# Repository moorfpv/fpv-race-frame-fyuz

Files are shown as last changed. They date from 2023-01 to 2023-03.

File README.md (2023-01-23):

# FYUZ - FPV Open Source 5" Race Frame

Bau dir deinen eigenen Race Copter für 16mm oder 12mm Lochkreis Motoren mit dem FYUZ Rahmenset. Die Carbon-Bauteile sind mit geringst möglichem Herstellungsaufwand zu produzieren.  

fyuz_s300

## Frame-Spec
* Propbase: 5"  
* Bottomplate: 2mm
* Midplate: 2mm
* Toplate: 2mm
* Armhook: 2mm or 3mm
* Arms: 4mm or 5.5mm
* AIO-Mount: 2mm, for M2, for 25.5 x 25.5 AIO Boards
* Lipopad: 2mm Moosgummi
* Stack mounting: 20 x 20 (for M2 or M3 screws)
* Standoff distance: 20mm
* Weight 5" with 20mm Alu Standoffs:  
  * with 4mm Arms for Motormount 12mm: 43.5g  
  * with 5.5mm Arms for Motormount 16mm: 56.2g  

## Carbon Parts

### 2mm Plate
* Bottomplate-H2.0.dxf  
* Midplate-M2-Stack-H2.0.dxf  
* Midplate-M3-Stack-H2.0.dxf  
* Topplate-H2.0.dxf  
* AIO-Mount-M2-StackMount-H2.0.dxf  
* Armhook-H2.0.dxf (Motormount 12mm)  

### 3mm Plate
* Armhook-H3.0.dxf (Motormount 16mm)  

### 4mm Arms
* 4x-715.70-H4.0.dxf (Motormount 12mm)  

### 5.5mm Arms
* 4x-720.76-H5.5.dxf (Motormount 16mm)  

## Buy Carbon - only Top producer/dealer
* [AHLtec](https://www.ahltec.de/shop/de/); optional mit Fräs-Service - Germany  
* [www.ikabon.com](https://www.ikabon.com); [email, Wendy Chan](mailto:info@ikabon.com) - China  
* [www.jinjiuyi.net](http://www.jinjiuyi.net); [email](mailto:info@jinjiuyi.net) - China  

## Laser Parts
* LipoPad.dxf

## Screws & Nuts

* countersunk head screw 4x M3 x 16  
* countersunk head screw 4x M3 x 6  
* pressnut 6x M3; [Buy](https://www.copterfarm.de/einpressmuttern-m3-10er-set-521.html) - Germany  

### For Fyuz Sub300 - Motormount 12mm
* countersunk head screw 2x M3 x 10

### For Fyuz - Motormount 16mm
* countersunk head screw 2x M3 x 12

### For AIO Mount
* lens head screw 4x M2 x 12 | 8 | 6

# Betaflight Presets - EXPERIMENTAL
* [BF 4.3 Presets for FyuzS300](https://github.com/moorfpv/betaflight-presets)
* [How to use Presets](https://betaflight.de/docs/knowledge-base/hintergrundwissen/betaflight-presets/)

# License

Creative Commons (4.0 International License) Attribution - NonCommercial - Share Alike (https://creativecommons.org/licenses/by-nc-sa/4.0/deed.en)

This work (DXF-Files) is licensed under a [Creative Commons (4.0 International License) Attribution - NonCommercial - Share Alike](https://creativecommons.org/licenses/by-nc-sa/4.0/deed.en).  

✖ | Sharing without ATTRIBUTION  
✔ | Remix Culture allowed  
✖ | Commercial Use  
✖ | Free Cultural Works  
✖ | Meets Open Definition  

# See also
* [Fyuz S300 Printables](https://www.printables.com/model/322457-sub300fpv-fyuz/files)  
* [screwsandmore](https://www.screwsandmore.de/en) - Germany  
* [five33 Printables](https://www.printables.com/model/243738-five33-lightswitch)  

---



* Arms: 4mm  
* Armhook: 2mm
* Weight 5" with 20mm Alu Standoffs: 43.5g  

Sources: [Arm-Parts/Motormount-12mm](https://github.com/moorfpv/fpv-race-frame-fyuz/tree/master/Arm-Parts/Motormount-12mm)  

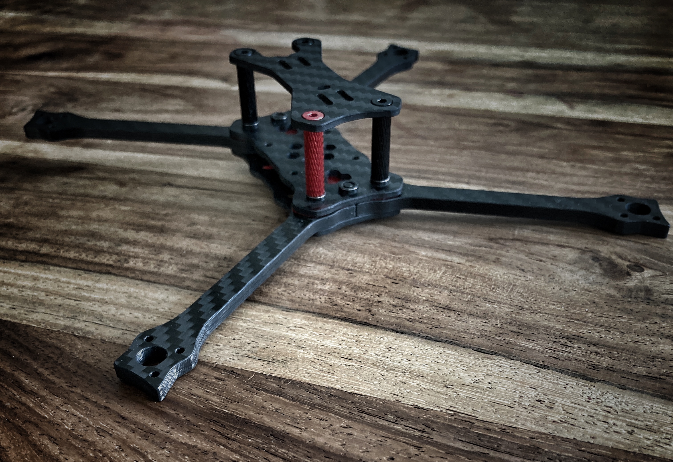
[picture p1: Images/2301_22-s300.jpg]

---
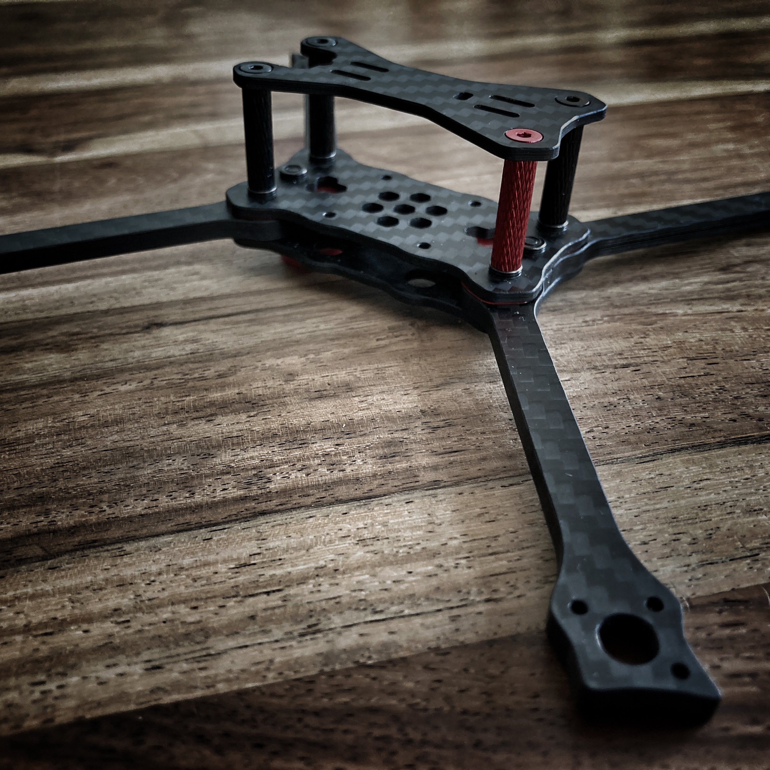
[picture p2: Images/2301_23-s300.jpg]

---


---  
---  



* Arms: 5.5mm  
* Armhook: 3mm
* Weight 5" with 20mm Alu Standoffs: 56.2g  

Sources: [Arm-Parts/Motormount-16mm](https://github.com/moorfpv/fpv-race-frame-fyuz/tree/master/Arm-Parts/Motormount-16mm)  

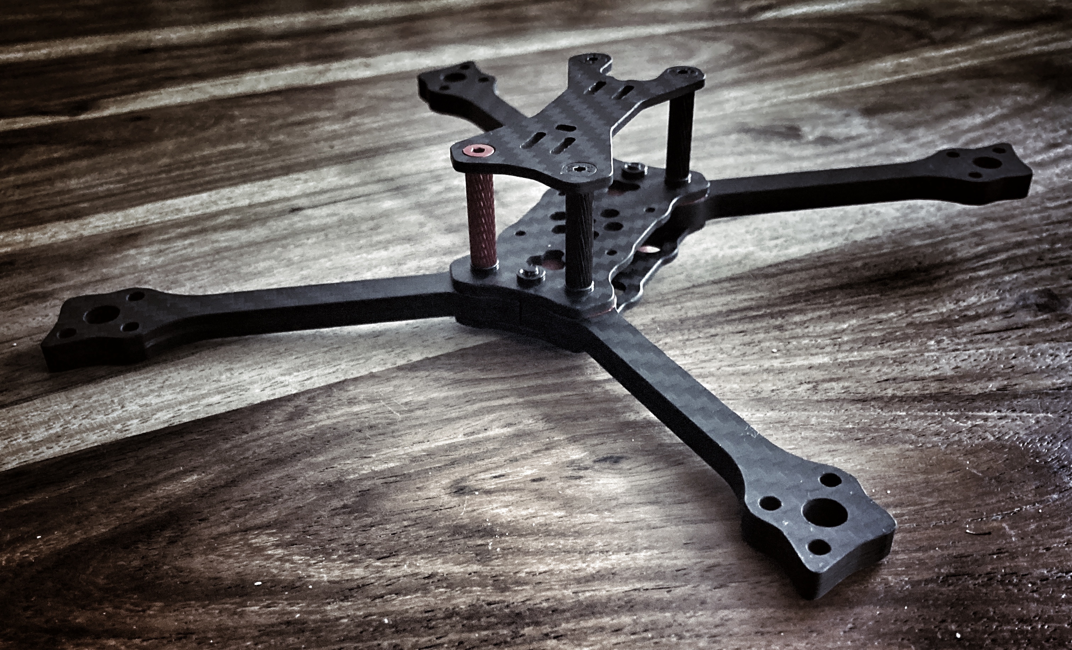
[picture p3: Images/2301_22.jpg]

---
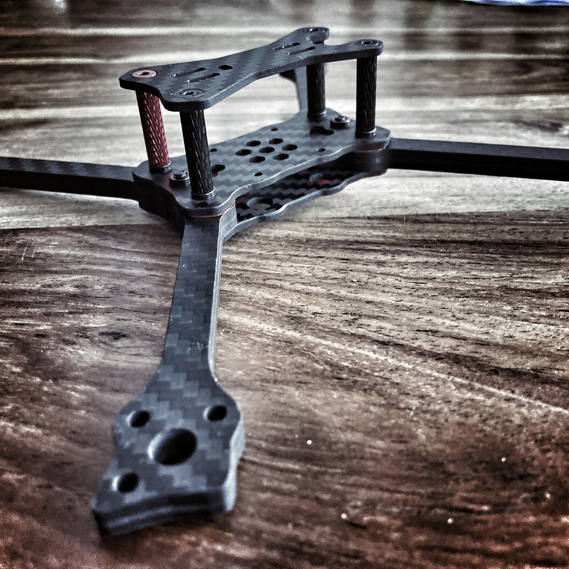
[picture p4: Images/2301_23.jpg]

---


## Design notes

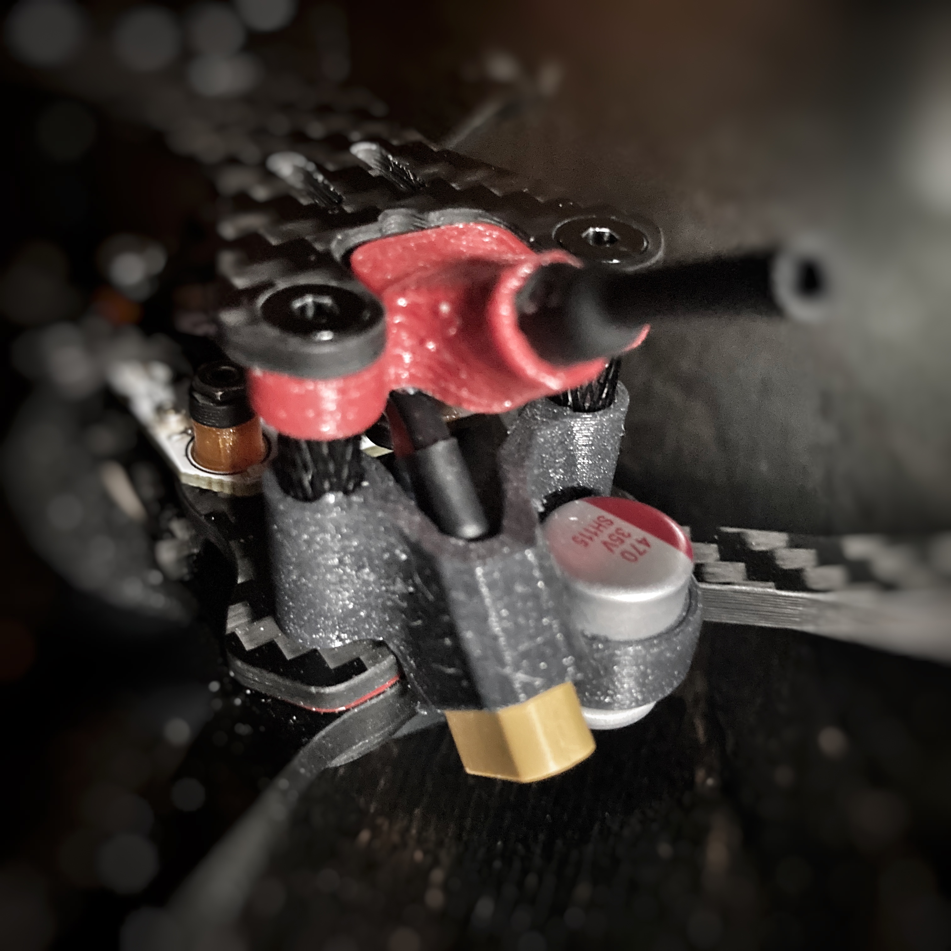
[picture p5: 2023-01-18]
Images/2301_02-s300.jpg

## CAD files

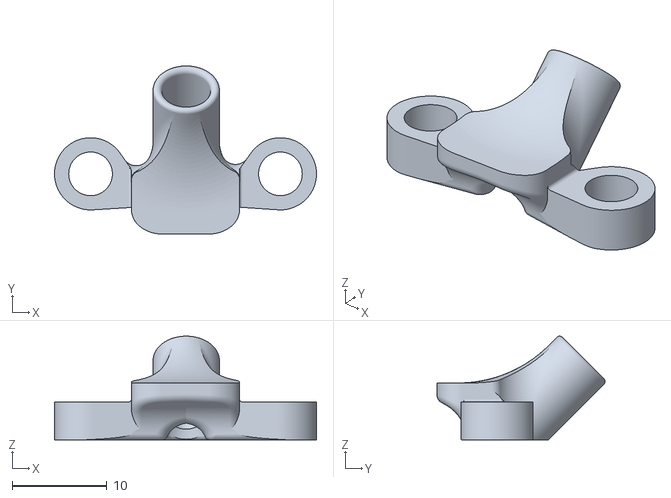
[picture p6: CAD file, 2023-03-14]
3D-Parts/TPU/Fyuz-TBS-Linear-VtxAntenna-Mount-v2.1.stl
27.6 x 17.7 x 10.9

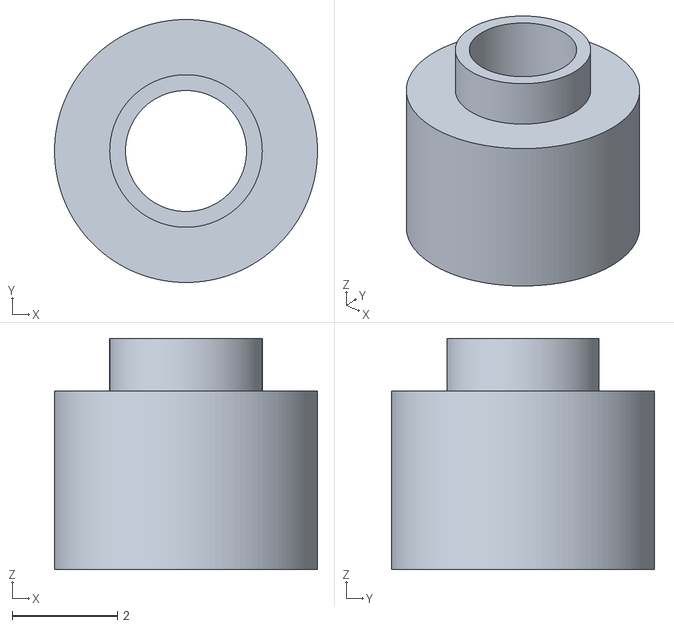
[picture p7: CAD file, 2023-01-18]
AIO-Mount/3D-Parts/ASA_Nozzle-0.2/AIOmount-Spacer-M2-H3.4.stl
5.00 x 5.00 x 4.40

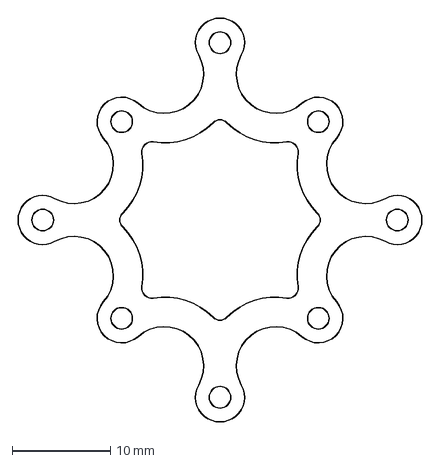
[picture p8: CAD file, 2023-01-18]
AIO-Mount/CNC-Parts/AIO-Mount-M2-StackMount-H2.0.dxf
41.4 x 41.4 mm

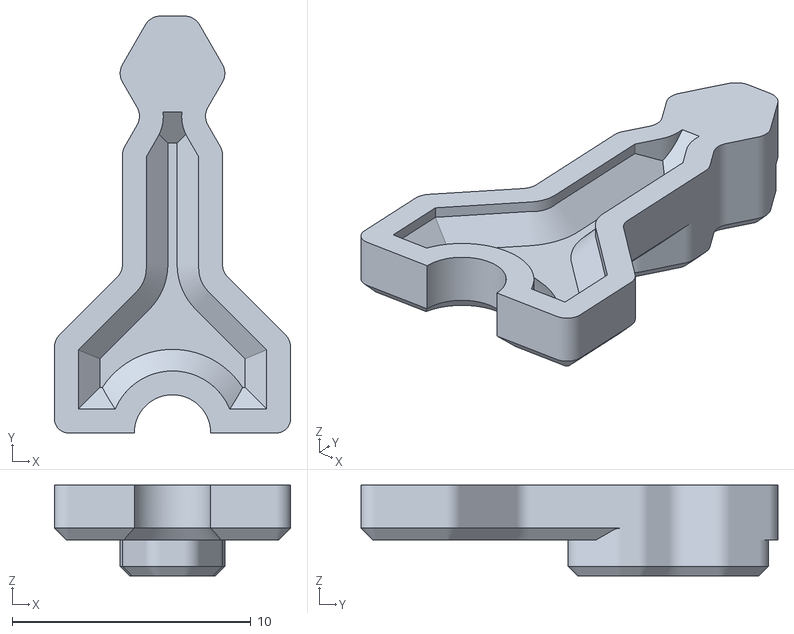
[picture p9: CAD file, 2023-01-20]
Arm-Parts/Motormount-12mm/3D-Parts/TPU/Peezer-v2-Armhook-H2.0-Arm-H4.0.stl
9.90 x 17.5 x 3.80

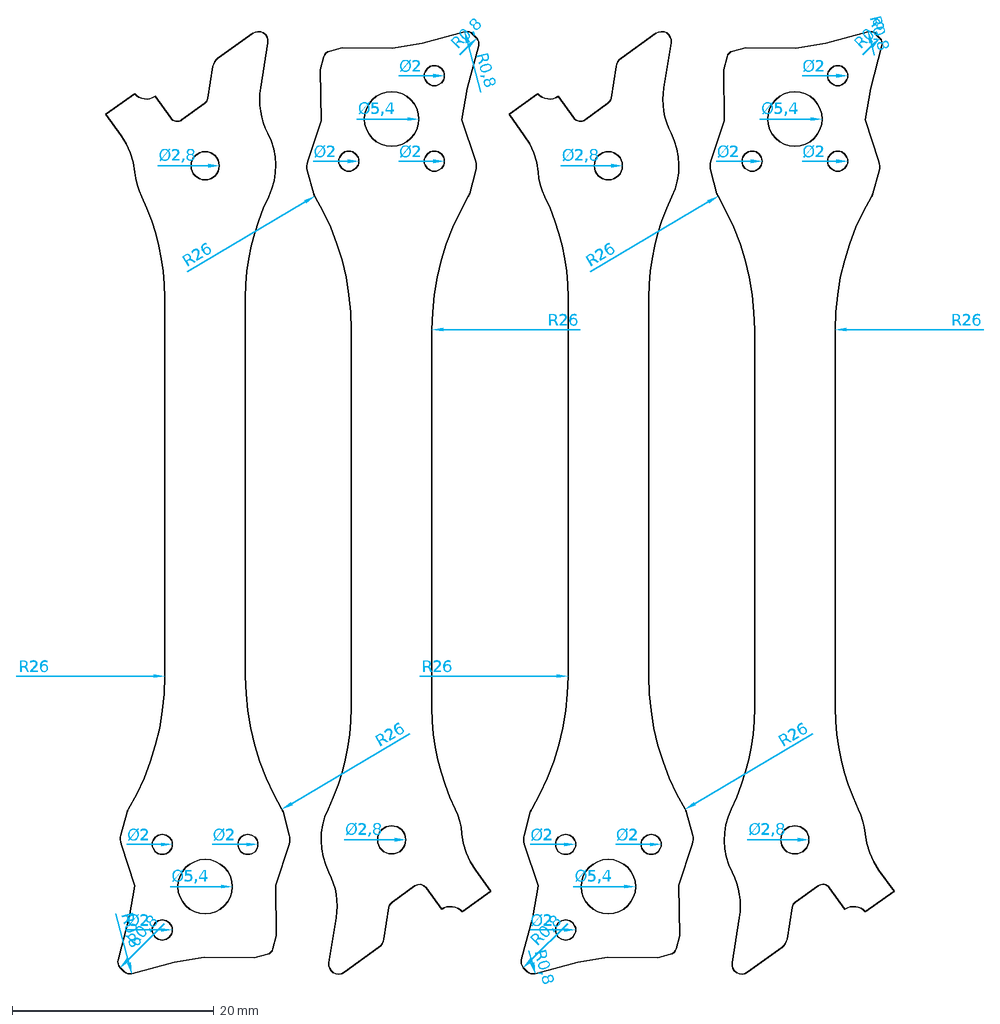
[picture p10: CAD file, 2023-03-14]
Arm-Parts/Motormount-12mm/CNC-Parts/5inch/4x-715.80.dxf
R0,8
R26
Ø2
Ø5,4
Ø2,8

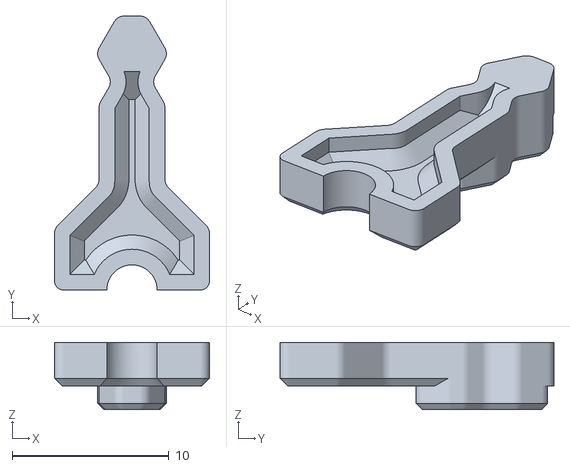
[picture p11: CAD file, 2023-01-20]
Arm-Parts/Motormount-16mm/5inch/3D-Parts/TPU/Peezer-v2-Armhook-H3.0-Arm-H5.5.stl
9.90 x 17.5 x 4.30

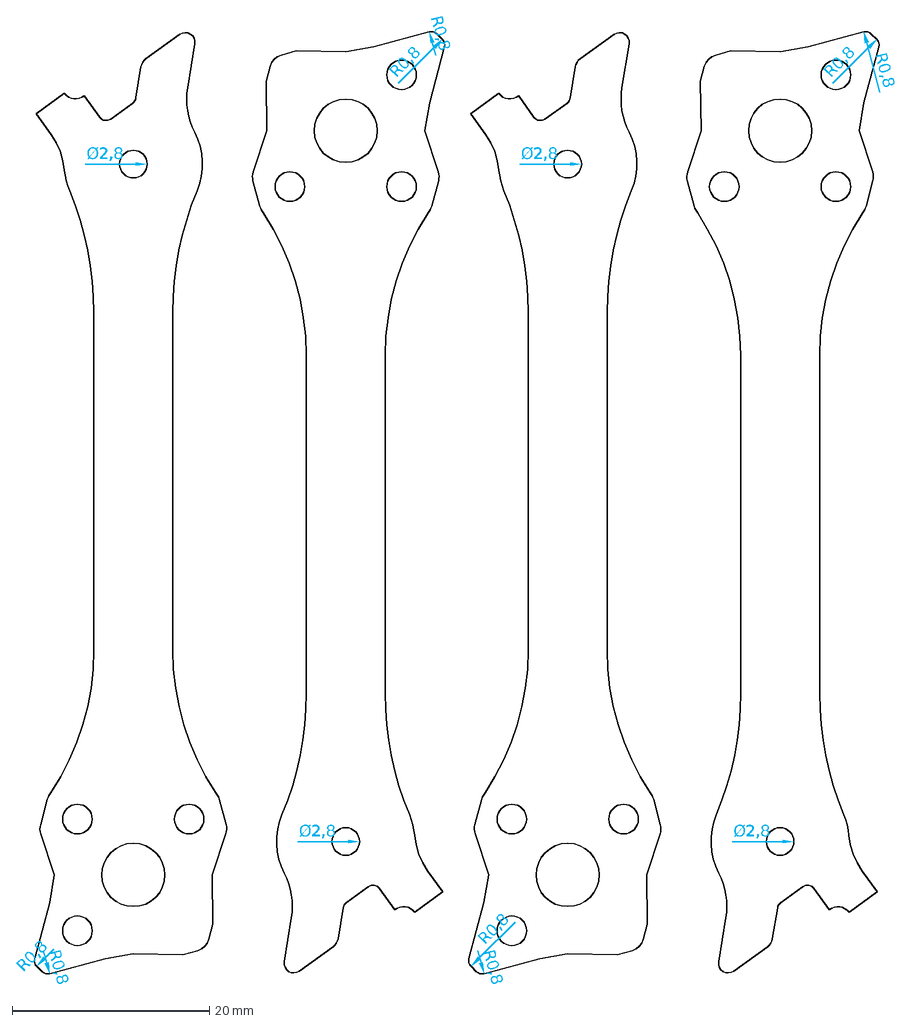
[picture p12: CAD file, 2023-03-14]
Arm-Parts/Motormount-16mm/5inch/CNC-Parts/4x-720.80.dxf
R0,8
Ø2,8

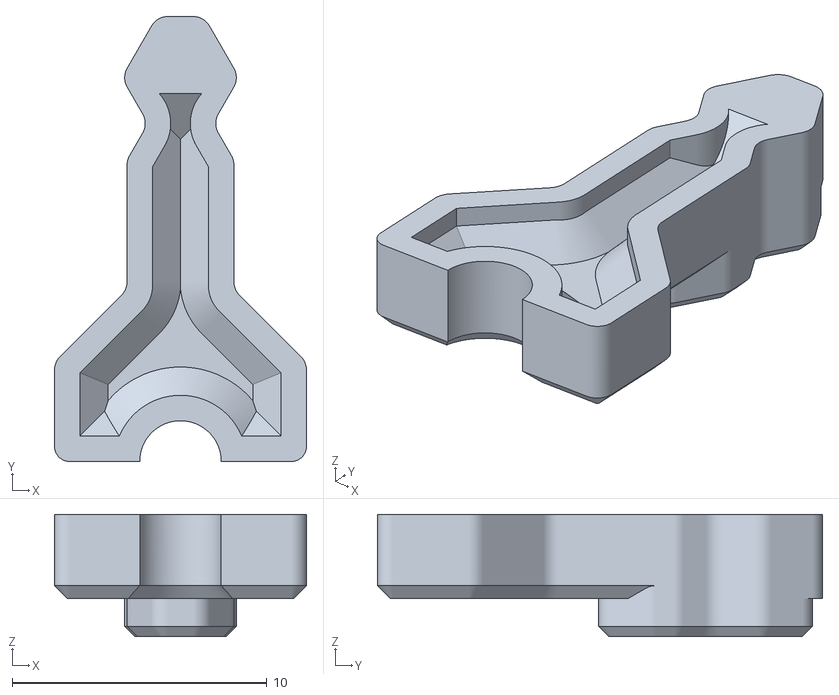
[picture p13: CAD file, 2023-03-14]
Arm-Parts/Motormount-16mm/6inch/3D-Parts/TPU/Peezer-v2-Armhook-H3.0-Arm-H6.0.stl
9.90 x 17.5 x 4.80

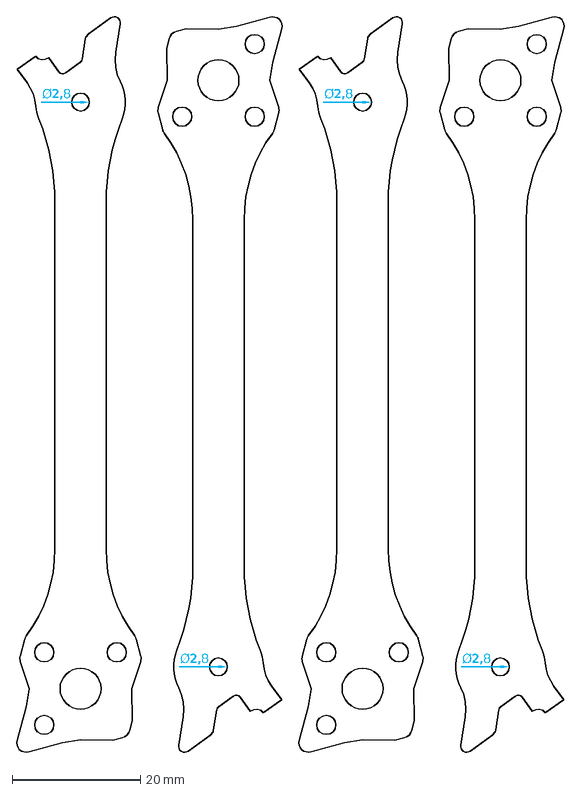
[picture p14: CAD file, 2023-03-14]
Arm-Parts/Motormount-16mm/6inch/CNC-Parts/4x-915.80.dxf
Ø2,8

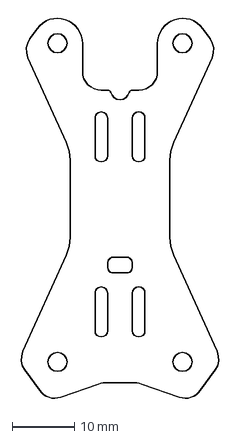
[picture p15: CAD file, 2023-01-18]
Body-Parts/CNC-Parts/Topplate-H2.0.dxf
32.0 x 61.4 mm

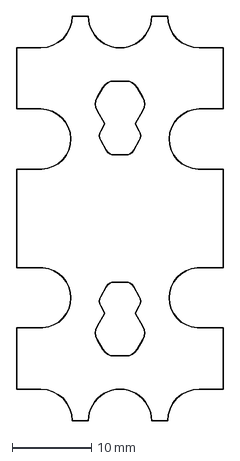
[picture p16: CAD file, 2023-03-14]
Body-Parts/Laser-Parts/Lipopad.dxf
26.1 x 51.0 mm

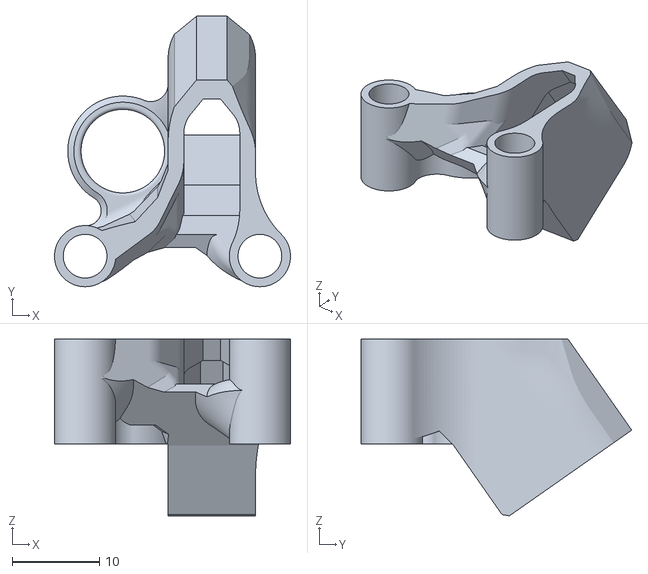
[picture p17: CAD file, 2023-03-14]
3D-Parts/TPU/Fyuz-XT60Plug-And-Cap-Mount-v3.stl
27.0 x 30.9 x 20.2

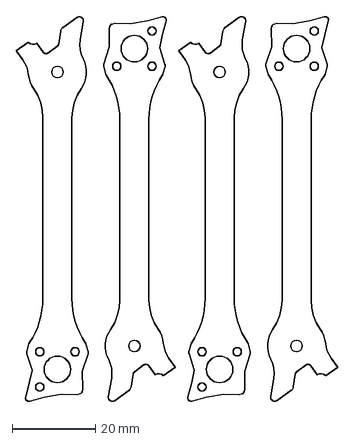
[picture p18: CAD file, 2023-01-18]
Arm-Parts/Motormount-12mm/CNC-Parts/5inch/4x-715.70.dxf
77.2 x 92.6 mm

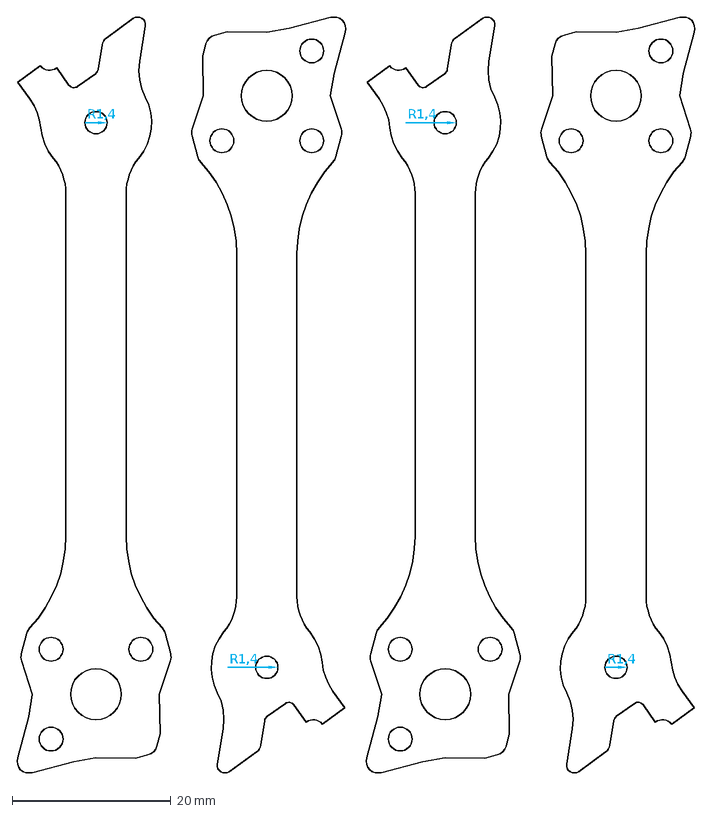
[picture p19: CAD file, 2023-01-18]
Arm-Parts/Motormount-16mm/5inch/CNC-Parts/4x-720.76.dxf
R1,4

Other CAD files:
Arm-Parts/Motormount-16mm/6inch/CNC-Parts/Armhook-H3.0.dxf
Body-Parts/CNC-Parts/Midplate-M3-Stack-H2.0.dxf
3D-Parts/TPU/Fyuz-Peezpad-v1.stl
Arm-Parts/Motormount-16mm/5inch/CNC-Parts/Armhook-H3.0.dxf
3D-Parts/TPU/Fyuz-Peezpad-PROTO.stl
3D-Parts/TPU/Fyuz-XT30Plug-And-Cap-Mount-v3.stl
3D-Parts/TPU/five33-CamMount-LS-20mm.stl
3D-Parts/TPU/five33-Fin-Tall.stl
3D-Parts/TPU/five33-WiggleEater-v2.stl
AIO-Mount/3D-Parts/ASA_Nozzle-0.2/AIOmount-Spacer-M2-H3.5.stl
AIO-Mount/3D-Parts/ASA_Nozzle-0.2/M2-Nut-H1.0.stl
AIO-Mount/3D-Parts/ASA_Nozzle-0.2/M2-Nut-H2.0.stl
Body-Parts/CNC-Parts/Bottomplate-H2.0.dxf
Body-Parts/CNC-Parts/Midplate-M2-Stack-H2.0.dxf

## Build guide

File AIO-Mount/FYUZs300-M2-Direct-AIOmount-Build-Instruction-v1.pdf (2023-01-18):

## fyuzs300

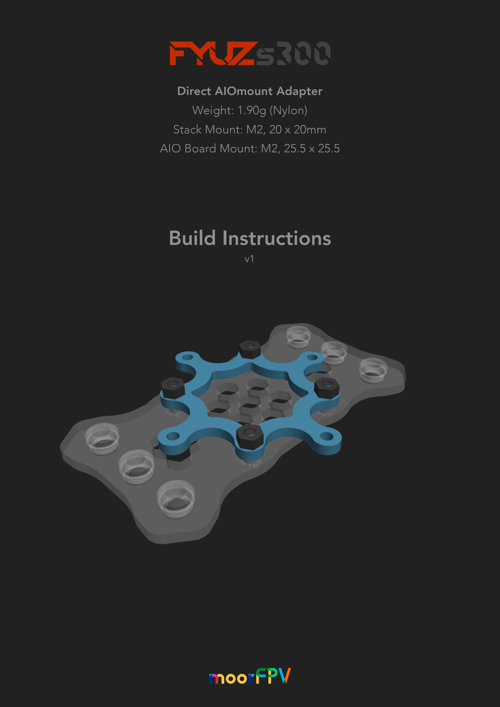
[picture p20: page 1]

Direct AIOmount Adapter
Weight: 1.90g (Nylon)
Stack Mount: M2, 20 x 20mm AIO Board Mount: M2, 25.5 x 25.5

### Build Instructions

v1

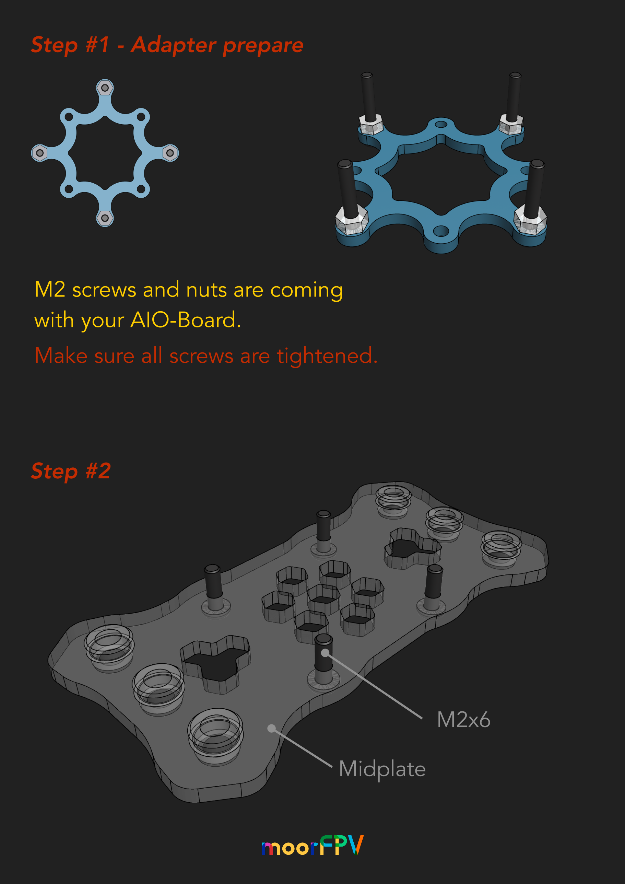
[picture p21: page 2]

Step #1 - Adapter prepare

Step #2

M2 screws and nuts are coming with your AIO-Board.
Make sure all screws are tightened.

M2x6

Midplate

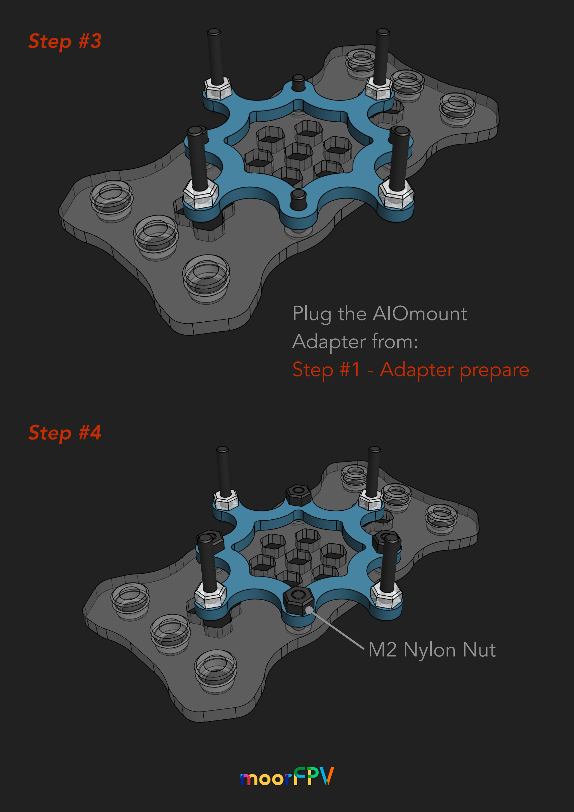
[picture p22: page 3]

Step #3

Step #4

M2 Nylon Nut

Plug the AIOmount
Adapter from:
Step #1 - Adapter prepare

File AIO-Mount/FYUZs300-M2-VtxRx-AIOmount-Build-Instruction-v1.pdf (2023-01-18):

## fyuzs300

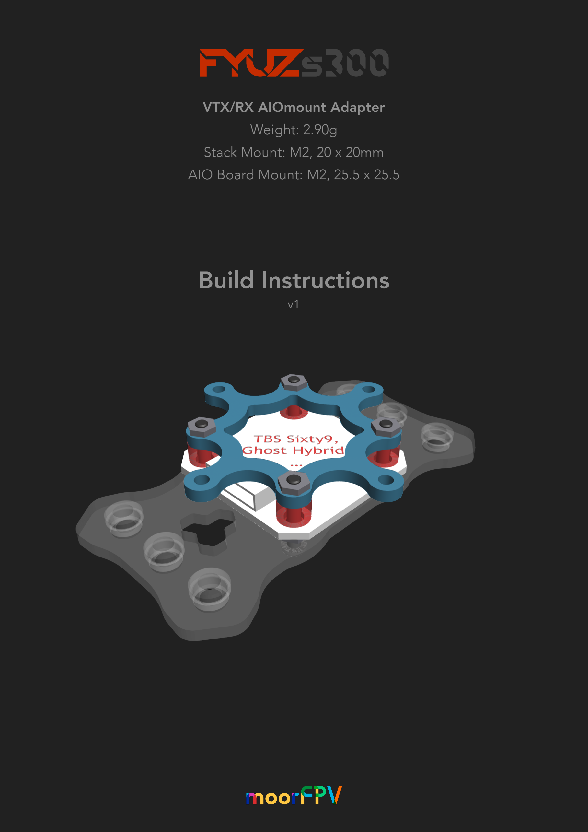
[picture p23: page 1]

VTX/RX AIOmount Adapter
Weight: 2.90g
Stack Mount: M2, 20 x 20mm AIO Board Mount: M2, 25.5 x 25.5

### Build Instructions

v1

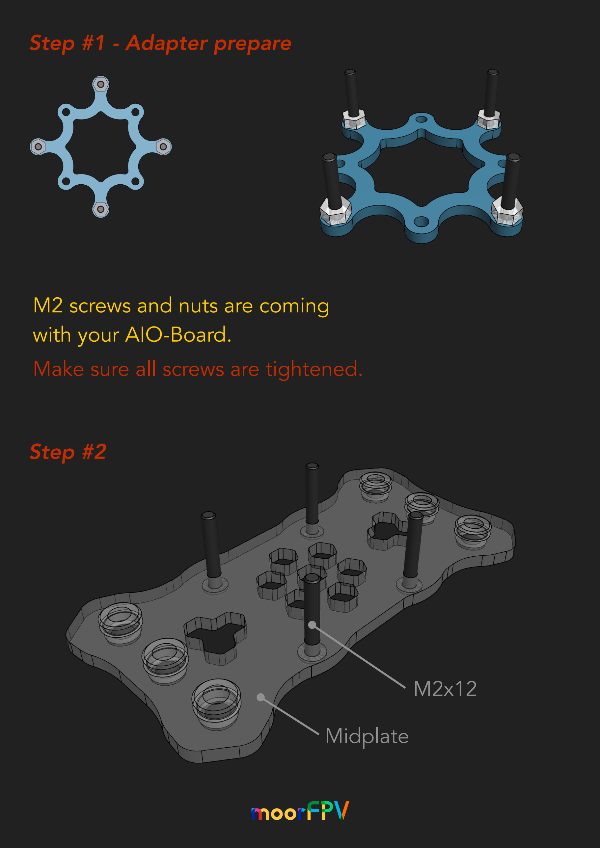
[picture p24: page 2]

Step #1 - Adapter prepare

Step #2

M2x12

Midplate

M2 screws and nuts are coming with your AIO-Board.
Make sure all screws are tightened.

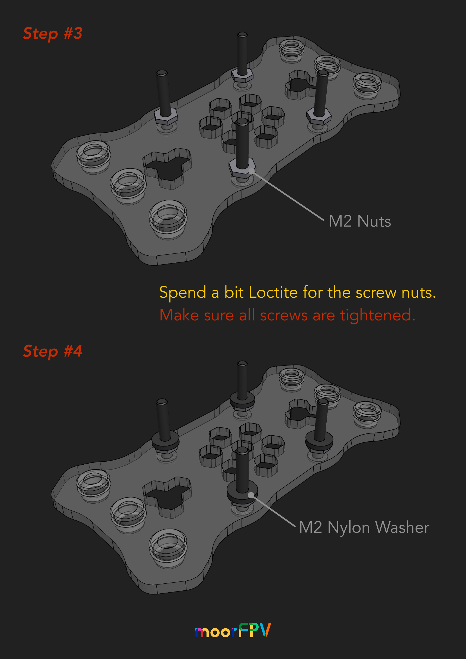
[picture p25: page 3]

Step #3

Step #4

M2 Nuts

M2 Nylon Washer

Spend a bit Loctite for the screw nuts. Make sure all screws are tightened.

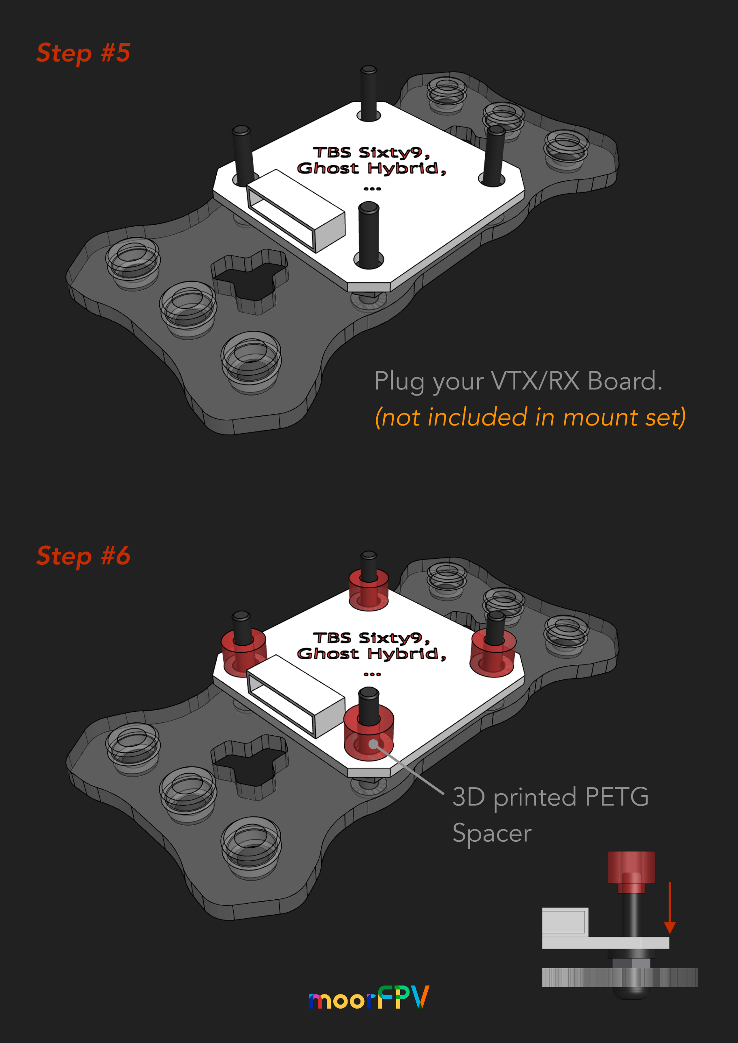
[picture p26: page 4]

Step #5

Step #6

Plug your VTX/RX Board.
(not included in mount set)

3D printed PETG
Spacer

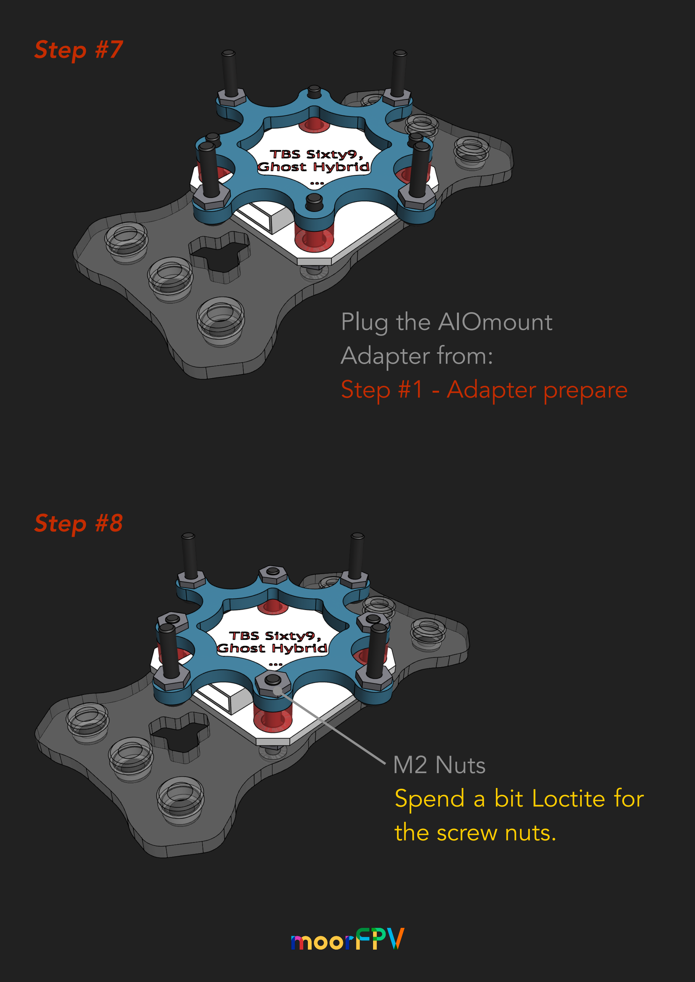
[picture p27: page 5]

Step #7

Step #8

Plug the AIOmount
Adapter from:
Step #1 - Adapter prepare

M2 Nuts
Spend a bit Loctite for
the screw nuts.

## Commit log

2023-01-18 Add some files initial;
    [4x-715.70-H4.0.dxf, 4x-720.76-H5.5.dxf, AIO-Mount-M2-StackMount-H2.0.dxf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]
2023-01-20 Add improved v2 Peezer STLs;
    [Peezer-v1-Armhook-H2.0-Arm-H4.0.stl, Peezer-v2-Armhook-H2.0-Arm-H4.0.stl, Peezer-v2-Armhook-H3.0-Arm-H5.5.stl]
2023-01-20 Remove v1 Peezer STLs;
    [Peezer-v1-Armhook-H2.0-Arm-H4.0.stl, Peezer-v1-Armhook-H3.0-Arm-H5.5.stl]
2023-03-14 Add new Arms and TPU print parts;
    * [new] 6inch Arms
    * [new] Peezer-v2-Armhook-H3.0-Arm-H6.0.stl
    * [improved] more durable 5inch Arms (16mm Motormount)
    * [improved] more durable 5inch Arms (12mm Motormount)
    * [new] Fyuz-XT60Plug-And-Cap-Mount-v3.stl
    * [improved] Fyuz-TBS-Linear-VtxAntenna-Mount-v2.1.stl
    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
    [4x-715.70.dxf, 4x-715.80.dxf, 4x-720.76.dxf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]
